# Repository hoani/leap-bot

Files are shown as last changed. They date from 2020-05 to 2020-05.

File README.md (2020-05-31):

##  Revision 0.0.0

[Production Package](./release/rev-0-0-0.zip)

### Pinout Allocation

| GPIO Pin | Usage | Function |
|---|-----|---|
| 25 | PWM | Motor1 drive1 |
| 26 | PWM | Motor1 drive2 |
| 33 | INPUT | Motor1 nFault |
| 27 | INPUT | Encoder1 A |
| 14 | INPUT | Encoder1 B |
| 35 | PWM | Motor2 drive1 |
| 32 | PWM | Motor2 drive2 |
| 34 | INPUT | Motor2 nFault |
| 19 | INPUT | Encoder2 A |
| 18 | INPUT | Encoder2 B |
|  7 | OUTPUT | Power Front Light Sensors |
| 13 | ADC2-4 | Front-Left Light Sensor |
| 15 | ADC2-3 | Front Level Sensor |
| 36 | ADC1-0 | Front-Right Light Sensor |
|  8 | OUTPUT | Power Back Light Sensors |
| 12 | ADC2-5 | Back-Left Light Sensor |
|  2 | ADC2-2 | Back Level Sensor |
|  4 | ADC2-0 | Back Right Level Sensor
|  3 | UART | Prog_TX |
|  1 | UART | Prog_RX |
|  6 | OUTPUT | LED0 |
|  9 | OUTPUT | LED1 |
| 22 | OUTPUT | LED2 |
| 16 | OUTPUT | LED3 |
| 11 | OUTPUT | LED4 |
| 10 | OUTPUT | LED5 |
| 21 | OUTPUT | LED6 |
| 23 | OUTPUT | LED7 |
| 39 |  | - |
|  0 | BOOT | - |
| 17 |  | - |
|  5 |  | - |

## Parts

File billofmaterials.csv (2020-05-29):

Reference | Quantity | Value | PartNumber | Notes
C1 | 1 | 10nF | C0805C103K5RAC7210
C12 C13 C2 C4 C7 C11 C8 C10 C9 C16 | 10 | 100nF | C0805C104M5RACTU
C14 C15 C6 C5 C3 | 5 | 4.7uF | GRM219R61E475MA73D
C17 C18 | 2 | 22uF | GRM21BR61A226ME51L
D1 D2 D3 D4 | 4 | BLUE | APT2012LVBC/D
D10 | 1 | GREEN | LTST-C170KGKT
D11 D12 | 2 | YELLOW | LY R976-PS-36
D6 D5 D8 D7 | 4 | RED | LH R974-LP-1
D9 | 1 | BAT54C | BAT54C
FB1 | 1 | MPZ2012S101AT000 | MPZ2012S101AT000
J1 | 1 | 6.29105E+11 | 6.29105E+11
J2 | 1 | Conn_01x04_Male | B4B-XH-A(LF)(SN)
J4 J3 | 2 | BM06B-SRSS-TB | BM06B-SRSS-TB(LF)(SN)
L1 | 1 | 33uH, 1.7A | SRN8040-330M
Q1 Q2 | 2 | FDV301N | FDV301N
R13 R14 R15 R23 R24 R25 | 6 | 33k | RC0805FR-0733KL
R2 R3 R4 R5 | 4 | 56R | RC0805FR-0756RL
R22 R30 R26 R27 | 4 | 10k | RNCP0805FTD10K0CT-ND
R31 R32 | 2 | 0R22 | KRL1632E-M-R220-F-T5
R7 R16 R17 R6 R9 R8 R10 R11 R12 R19 R20 R21 R28 R29 R18 | 15 | 100R | RC0805FR-07100RL
RN1 | 1 | 27R | EXB-V4V270JV
SW1 SW2 | 2 | 1825910-6 | 1825910-6
U1 U2 U3 U6 U7 U8 | 6 | QRE1113GR | QRE1113GR
U10 U11 | 2 | DRV8872DDA | DRV8872DDA
U4 | 1 | ADP2302ARDZ-3.3 | ADP2302ARDZ-3.3
U5 | 1 | FT230XS | FT230XS
U9 | 1 | ESP32-WROOM-32D | ESP32-WROOM-32D
H1 H2 | 2 | Motor Cable | A06SR06SR30K51B
M1 M2 | 2 | Pololu Motor 12V 650RPM | 3050
E1 | 1 | Pololu Encoder pair | 4761
W1 W2 | 2 | Wheels |  | Order from https://www.aliexpress.com/item/32854636812.html
S1 S2 | 2 | Ball Screw M4x16mm |  | Order from https://www.aliexpress.com/item/4000370370791.html
B1 | 1 | 3S 500mAh LIPO Battery |  | Order from https://hobbyking.com/en_us/zippy-compact-500mah-3s-25c-lipo-pack.html

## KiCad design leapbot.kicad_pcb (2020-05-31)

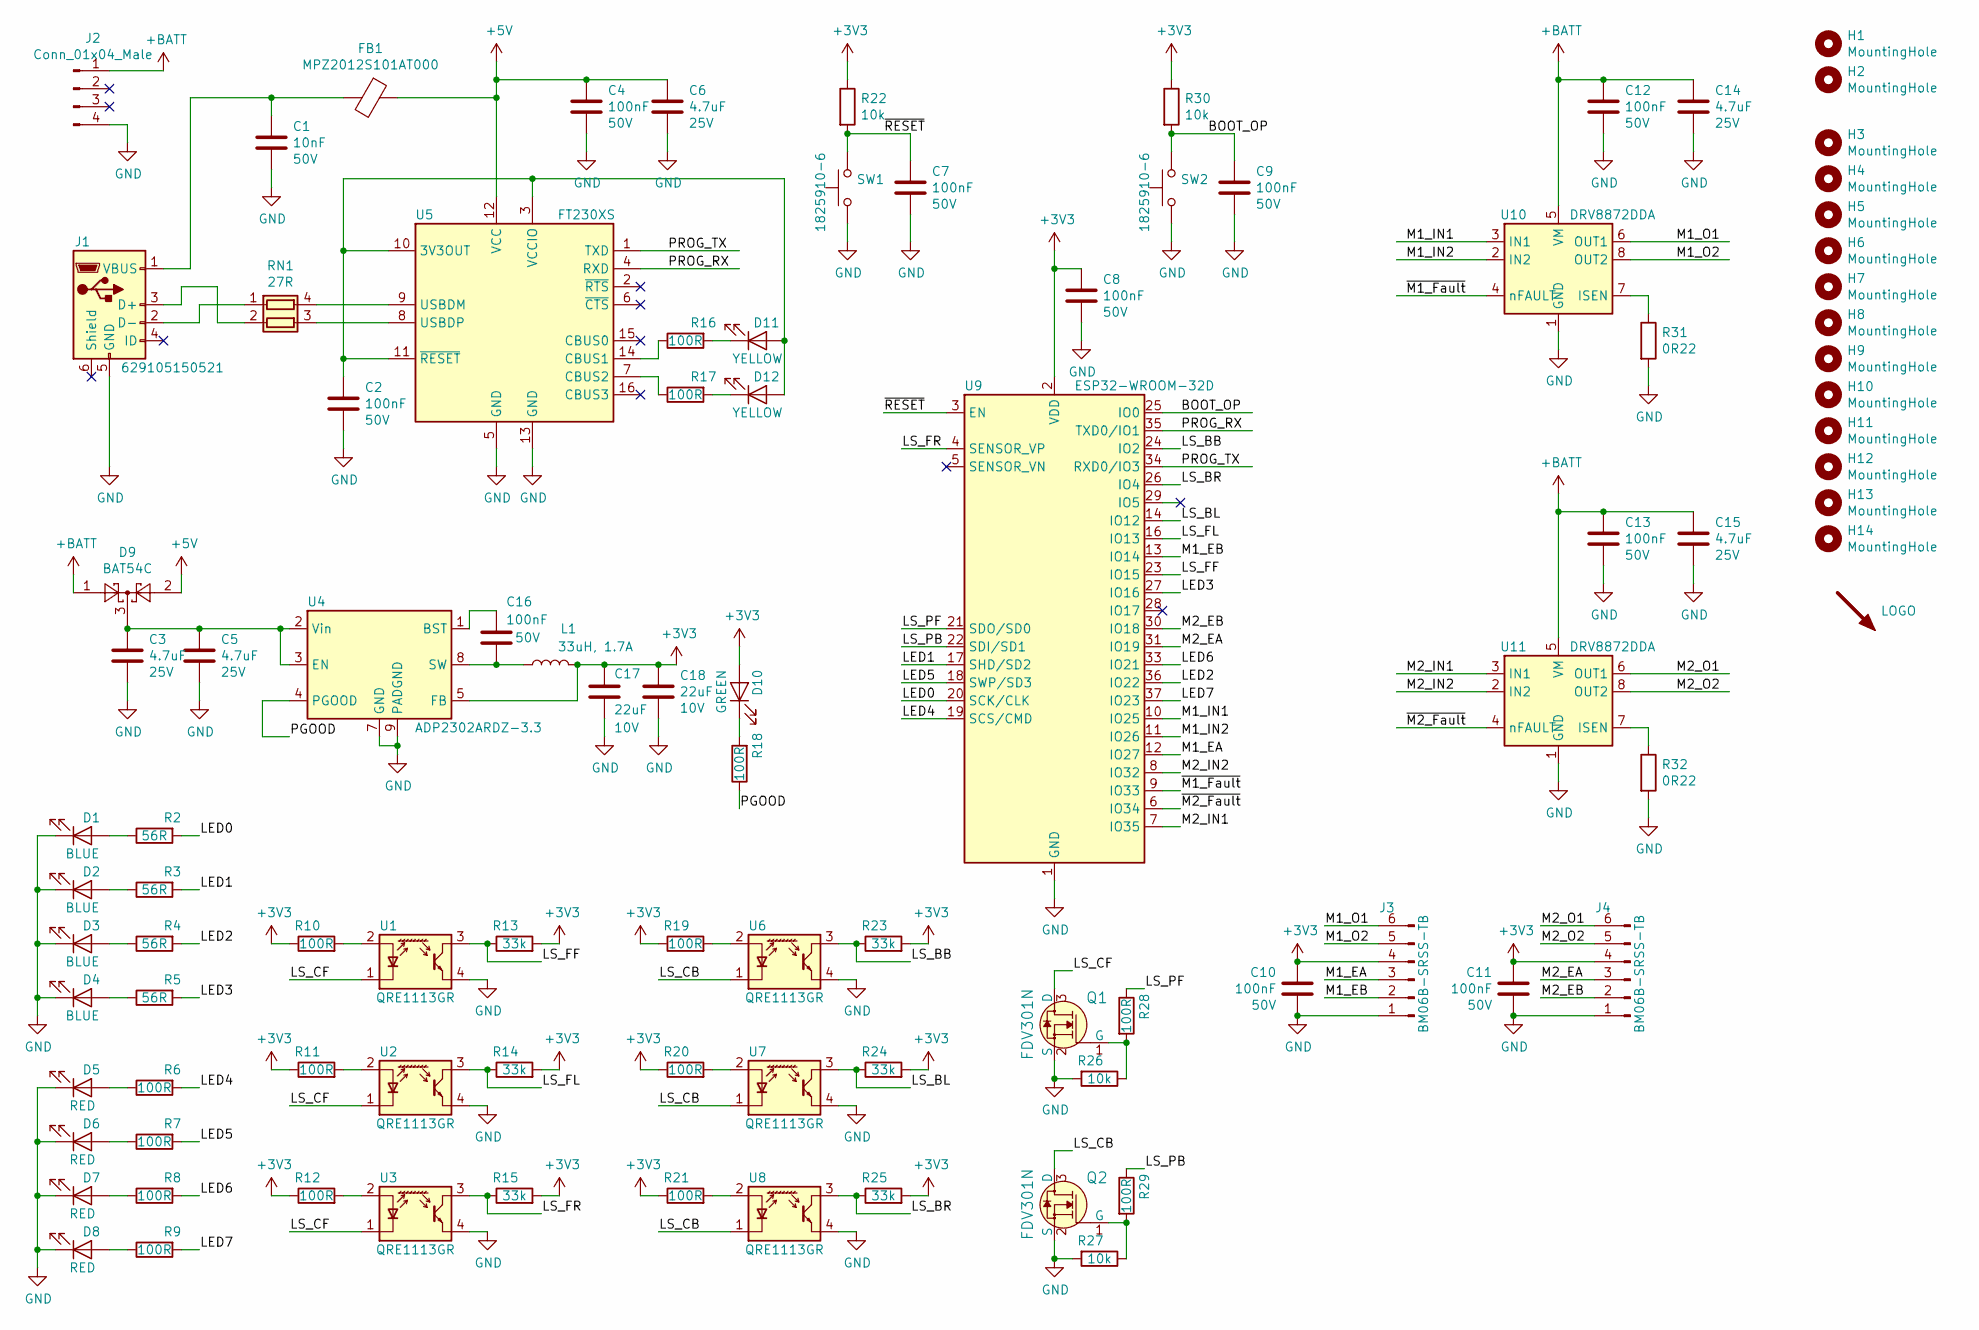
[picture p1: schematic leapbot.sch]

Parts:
C1: 10nF; C_0805_2012Metric; Voltage 50V; PartNumber C0805C103K5RAC7210
C2, C4, C7, C8, C9, C10, C11, C12, C13, C16: 100nF; C_0805_2012Metric; Voltage 50V; PartNumber C0805C104M5RACTU
C3, C5, C6, C14, C15: 4.7uF; C_0805_2012Metric; Voltage 25V; PartNumber GRM219R61E475MA73D
C17, C18: 22uF; C_0805_2012Metric; Voltage 10V; PartNumber GRM21BR61A226ME51L
D1, D2, D3, D4: BLUE; LED_0805_2012Metric_Castellated; PartNumber APT2012LVBC/D
D5, D6, D7, D8: RED; LED_0805_2012Metric_Castellated; PartNumber LH R974-LP-1
D9: BAT54C; SOT-23; PartNumber BAT54C
D10: GREEN; LED_0805_2012Metric_Castellated; PartNumber LTST-C170KGKT
D11, D12: YELLOW; LED_0805_2012Metric_Castellated; PartNumber LY R976-PS-36
FB1: MPZ2012S101AT000; R_0805_2012Metric; PartNumber MPZ2012S101AT000
H1, H2: MountingHole; MountingHole_4.3mm_M4
H3, H4, H5, H6, H7, H8, H9, H10, H11, H12, H13, H14: MountingHole; MountingHole_3.2mm_M3
J1: 629105150521; USB_Micro-B_Wuerth_629105150521_CircularHoles; PartNumber 629105150521
J2: Conn_01x04_Male; JST_XH_B4B-XH-A_1x04_P2.50mm_Vertical; PartNumber B4B-XH-A(LF)(SN)
J3, J4: BM06B-SRSS-TB; JST_SH_BM06B-SRSS-TB_1x06-1MP_P1.00mm_Vertical; PartNumber BM06B-SRSS-TB(LF)(SN)
L1: 33uH, 1.7A; L_Bourns-SRN8040_8x8.15mm; PartNumber SRN8040-330M
Q1, Q2: FDV301N; SOT-23; PartNumber FDV301N
R2, R3, R4, R5: 56R; R_0805_2012Metric; PartNumber RC0805FR-0756RL
R6, R7, R8, R9, R10, R11, R12, R16, R17, R18, R19, R20, R21, R28, R29: 100R; R_0805_2012Metric; PartNumber RC0805FR-07100RL
R13, R14, R15, R23, R24, R25: 33k; R_0805_2012Metric; PartNumber RC0805FR-0733KL
R22, R26, R27, R30: 10k; R_0805_2012Metric; PartNumber RNCP0805FTD10K0CT-ND
R31, R32: 0R22; R_1206_3216Metric; PartNumber KRL1632E-M-R220-F-T5
RN1: 27R; R_Array_Concave_2x0603; PartNumber EXB-V4V270JV
SW1, SW2: 1825910-6; SW_PUSH_6mm; PartNumber 1825910-6
SYM1: LOGO; logo
U1, U2, U3, U6, U7, U8: QRE1113GR; Everlight_ITR8307F43; PartNumber QRE1113GR
U4: ADP2302ARDZ-3.3; SOIC-8-1EP_3.9x4.9mm_P1.27mm_EP2.29x3mm; PartNumber ADP2302ARDZ-3.3
U5: FT230XS; SSOP-16_3.9x4.9mm_P0.635mm; PartNumber FT230XS
U9: ESP32-WROOM-32D; ESP32-WROOM-32; PartNumber ESP32-WROOM-32D
U10, U11: DRV8872DDA; Texas_HTSOP-8-1EP_3.9x4.9mm_P1.27mm_EP2.95x4.9mm_Mask2.4x3.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; PartNumber DRV8872DDA

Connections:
+3V3: C8.1, C10.2, C11.2, C17.1, C18.1, D10.2 (A), J3.4, J4.4, L1.2, R10.1, R11.1, R12.1, R13.2, R14.2, R15.2, R19.1, R20.1, R21.1, R22.1, R23.2, R24.2, R25.2, R30.1, U4.5 (FB), U9.2 (VDD)
+5V: C4.1, C6.1, D9.2, FB1.1, U5.12 (VCC)
+BATT: C12.1, C13.1, C14.1, C15.1, D9.1, J2.1, U10.5 (VM), U11.5 (VM)
/BOOT_OP: C9.1, R30.2, SW2.2, U9.25 (IO0)
/LED0: R2.2, U9.20 (SCK/CLK)
/LED1: R3.2, U9.17 (SHD/SD2)
/LED2: R4.2, U9.36 (IO22)
/LED3: R5.2, U9.27 (IO16)
/LED4: R6.2, U9.19 (SCS/CMD)
/LED5: R7.2, U9.18 (SWP/SD3)
/LED6: R8.2, U9.33 (IO21)
/LED7: R9.2, U9.37 (IO23)
/LS_BB: R23.1, U6.3 (C), U9.24 (IO2)
/LS_BL: R24.1, U7.3 (C), U9.14 (IO12)
/LS_BR: R25.1, U8.3 (C), U9.26 (IO4)
/LS_CB: Q2.3 (D), U6.1 (K), U7.1 (K), U8.1 (K)
/LS_CF: Q1.3 (D), U1.1 (K), U2.1 (K), U3.1 (K)
/LS_FF: R13.1, U1.3 (C), U9.23 (IO15)
/LS_FL: R14.1, U2.3 (C), U9.16 (IO13)
/LS_FR: R15.1, U3.3 (C), U9.4 (SENSOR_VP)
/LS_PB: R29.1, U9.22 (SDI/SD1)
/LS_PF: R28.1, U9.21 (SDO/SD0)
/M1_EA: J3.3, U9.12 (IO27)
/M1_EB: J3.2, U9.13 (IO14)
/M1_IN1: U9.10 (IO25), U10.3 (IN1)
/M1_IN2: U9.11 (IO26), U10.2 (IN2)
/M1_O1: J3.6, U10.6 (OUT1)
/M1_O2: J3.5, U10.8 (OUT2)
/M2_EA: J4.3, U9.31 (IO19)
/M2_EB: J4.2, U9.30 (IO18)
/M2_IN1: U9.7 (IO35), U11.3 (IN1)
/M2_IN2: U9.8 (IO32), U11.2 (IN2)
/M2_O1: J4.6, U11.6 (OUT1)
/M2_O2: J4.5, U11.8 (OUT2)
/PGOOD: R18.1, U4.4 (PGOOD)
/PROG_RX: U5.4 (RXD), U9.35 (TXD0/IO1)
/PROG_TX: U5.1 (TXD), U9.34 (RXD0/IO3)
/~M1_Fault: U9.9 (IO33), U10.4 (nFAULT)
/~M2_Fault: U9.6 (IO34), U11.4 (nFAULT)
/~RESET: C7.1, R22.2, SW1.2, U9.3 (EN)
GND: C1.2, C2.2, C3.2, C4.2, C5.2, C6.2, C7.2, C8.2, C9.2, C10.1, C11.1, C12.2, C13.2, C14.2, C15.2, C17.2, C18.2, D1.1 (K), D2.1 (K), D3.1 (K), D4.1 (K), D5.1 (K), D6.1 (K), D7.1 (K), D8.1 (K), J1.5 (GND), J2.4, J3.1, J4.1, Q1.2 (S), Q2.2 (S), R26.2, R27.2, R31.2, R32.2, SW1.1, SW2.1, U1.4 (E), U2.4 (E), U3.4 (E), U4.7 (GND), U4.9 (PADGND), U5.5 (GND), U5.13 (GND), U6.4 (E), U7.4 (E), U8.4 (E), U9.1 (GND), U9.15 (GND), U9.38 (GND), U9.39 (GND), U10.1 (GND), U10.9 (GND), U11.1 (GND), U11.9 (GND)
unnamed: C1.1, FB1.2, J1.1 (VBUS)
unnamed: C2.1, D11.2 (A), D12.2 (A), U5.3 (VCCIO), U5.10 (3V3OUT), U5.11 (~RESET)
unnamed: C3.1, C5.1, D9.3, U4.2 (Vin), U4.3 (EN)
unnamed: C16.1, U4.1 (BST)
unnamed: C16.2, L1.1, U4.8 (SW)
unnamed: D1.2 (A), R2.1
unnamed: D2.2 (A), R3.1
unnamed: D3.2 (A), R4.1
unnamed: D4.2 (A), R5.1
unnamed: D5.2 (A), R6.1
unnamed: D6.2 (A), R7.1
unnamed: D7.2 (A), R8.1
unnamed: D8.2 (A), R9.1
unnamed: D10.1 (K), R18.2
unnamed: D11.1 (K), R16.2
unnamed: D12.1 (K), R17.2
unnamed: J1.2 (D-), RN1.1 (R1.1)
unnamed: J1.3 (D+), RN1.2 (R2.1)
unnamed: Q1.1 (G), R26.1, R28.2
unnamed: Q2.1 (G), R27.1, R29.2
unnamed: R10.2, U1.2 (A)
unnamed: R11.2, U2.2 (A)
unnamed: R12.2, U3.2 (A)
unnamed: R16.1, U5.14 (CBUS1)
unnamed: R17.1, U5.7 (CBUS2)
unnamed: R19.2, U6.2 (A)
unnamed: R20.2, U7.2 (A)
unnamed: R21.2, U8.2 (A)
unnamed: R31.1, U10.7 (ISEN)
unnamed: R32.1, U11.7 (ISEN)
unnamed: RN1.3 (R2.2), U5.8 (USBDP)
unnamed: RN1.4 (R1.2), U5.9 (USBDM)

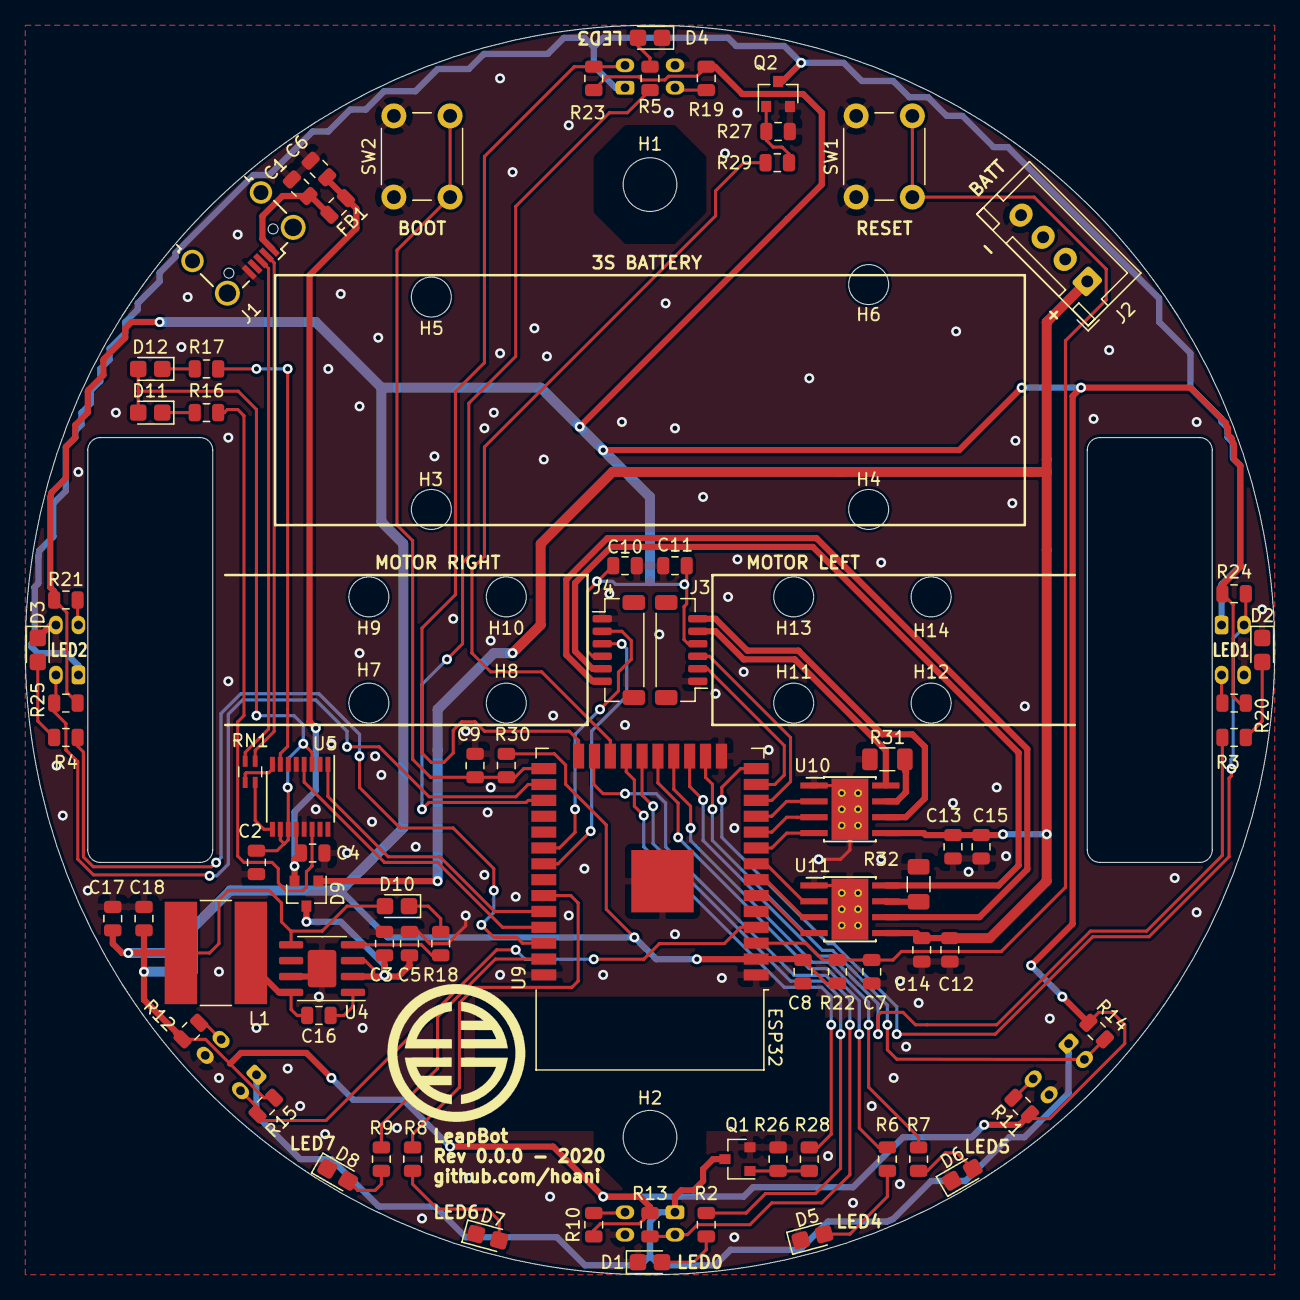
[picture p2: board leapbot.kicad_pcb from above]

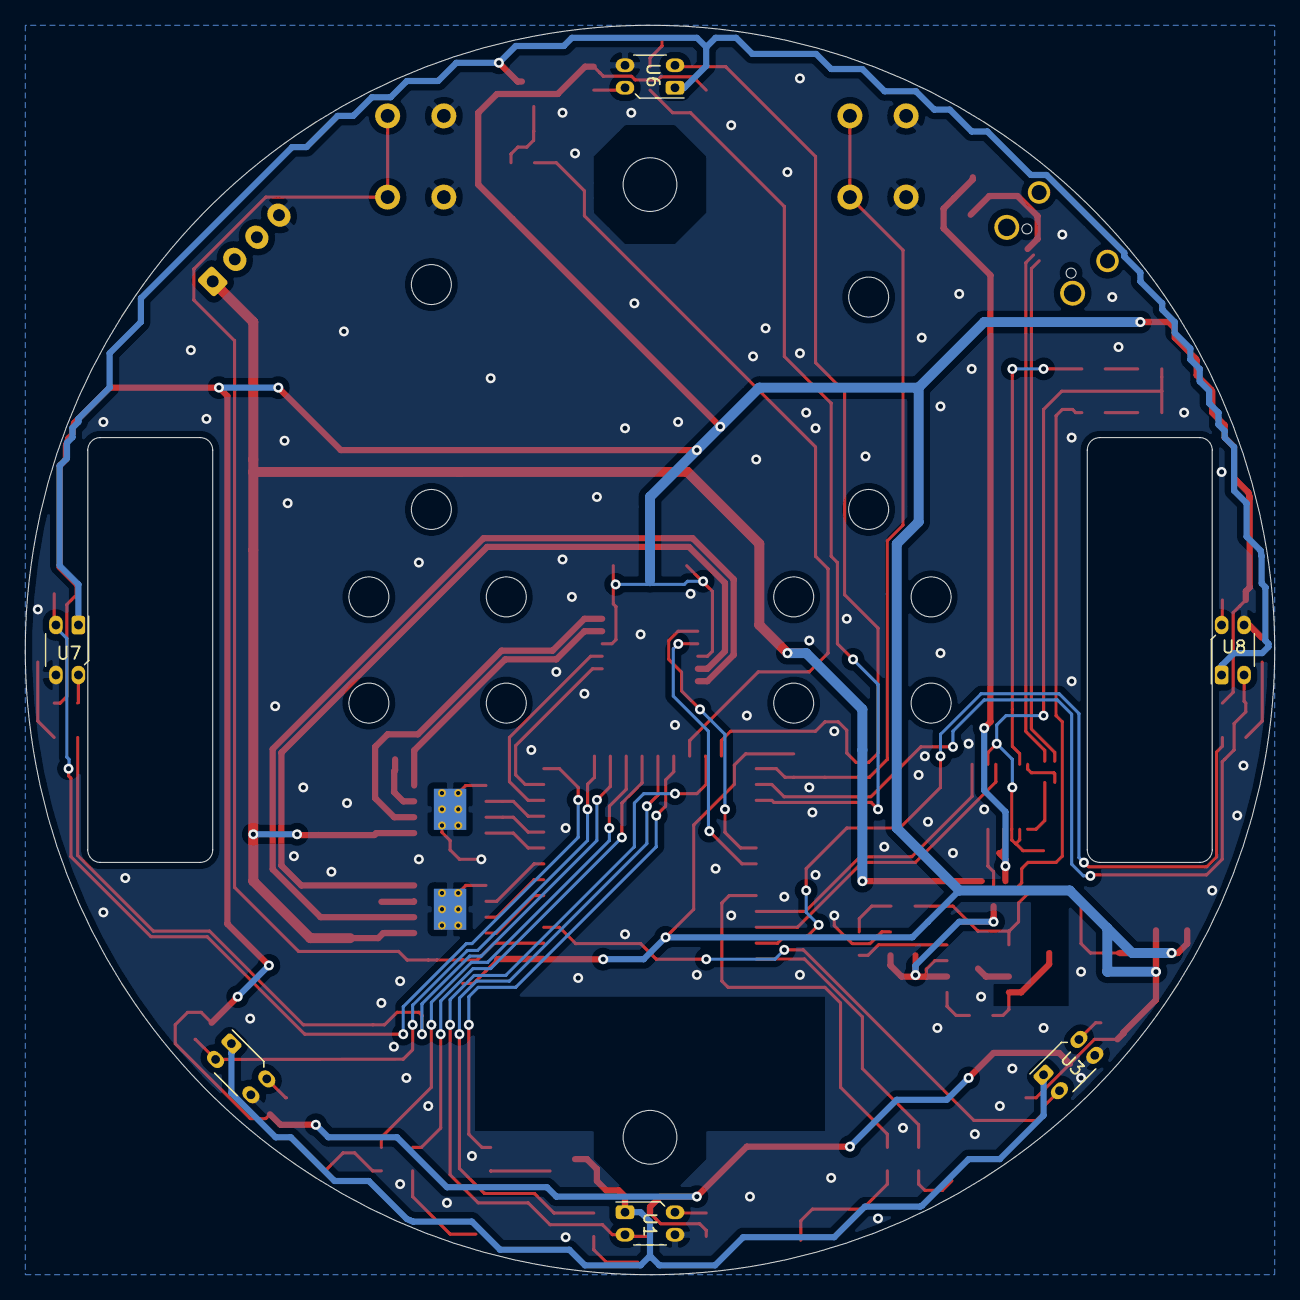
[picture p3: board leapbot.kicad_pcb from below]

Board: 2 copper layers, 100.0 x 100.0 mm, 98 parts (6 on the bottom side), 73 nets.

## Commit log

2020-05-29 First layout complete
    [leapbot.kicad_pcb, leapbot.sch]
2020-05-29 Add silkscreen annotations and logo, update titleblocks
    [leapbot.kicad_pcb, leapbot.sch]
2020-05-29 Add billofmaterials
    [billofmaterials.csv, leapbot.sch]
2020-05-31 Corrected some ADC assignments
    [leapbot.kicad_pcb, leapbot.sch]
